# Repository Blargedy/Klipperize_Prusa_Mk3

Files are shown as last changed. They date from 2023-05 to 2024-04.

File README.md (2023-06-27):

# Klipperize Prusa Mk3
This repo is for sharing the results of my efforts to upgrade the performance of my Prusa Mk3s. It is not a project aimed at mass adoption and therfore does not include modularity for individual variations in component selection.

That being said, I designed the printer to use the [Rapid Burner](https://github.com/chirpy2605/voron/tree/main/V0/Rapid_Burner) by [chirpy2605 aka waytotheweb](https://github.com/chirpy2605), which is designed to work with the Voron v0.2. This means that my mods will work with any design that is compatible with the Voron v0.2 tool mount. Chirpy has a wide array of options for hotends, fans, extruders, and LEDs, so by Chirpy's efforts my mod can accomodate most people's hardware choices. 

***This project is still a work-in-progress, so expect files to change until I am satisfied with the result.*** 





**My hardware configuration is as follows:**
* Rapid Burner in slideswipe configuration
* Rapido UHF
* Sherpa Mini with RIDGA modification
* EBB36 CANbus toolhead PCB
* SKR mini e3 v2
* Raspberry Pi 4 running Klipper

## Benefits
* The stock prusa toolhead weighs 550g, depending on how you weigh the wires and bearings. The Prusa adapted Rapid Burner weighs 334g, a weight saving of 216g
* The stock E3D V6 hotend has a volumetric flow limit of around 20 mm<sup>3</sup>/s, 25 mm<sup>3</sup>/s with a CHT nozzle. The Rapido UHF, with a 0.4mm Volcano nozzle has a flow limit of 24.1 mm<sup>3</sup>/s, 29 mm<sup>3</sup>/s with a CHT nozzle. Higher flow rate means faster prints. 
* Input Shaping
* Fan headers allow more fans, and are easy to control with software
* Klipper's error logging is extensive, unlike prusa's error logging
* Macros
* The part cooling fans of the Rapid Burner are stronger than the Mk3's single blower fan
* RGBLEDs go brr
* Can use buttons as triggers for code, making predetermined tasks such as preheat much faster
* Filament diameter compensation
* Easier object exclusion
* Finer control on heater/stepper turn off
* Wait on chamber thermistor for automatic chamber heating
* Finer control over bed mesh pattern

## BoM
* 3 x MLX 42021 female crimp 2 circuit recepticle [Digikey](https://www.digikey.ca/en/products/detail/molex/0050841020/134710)
* 3 x MLX 42022 male crimp 2 circuit recepticle [Digikey](https://www.digikey.ca/en/products/detail/molex/0050842022/2405413)
* 1 x MLX 42021 female crimp 4 circuit recepticle [Digikey](https://www.digikey.ca/en/products/detail/molex/0050841045/2405428)
* 1 x MLX 42022 male crimp 4 circuit recepticle [Digikey](https://www.digikey.ca/en/products/detail/molex/0050842042/2405411)
* 10 x MLX 36536 male crimps [Digikey](https://www.digikey.ca/en/products/detail/molex/0365360001/3185301)
* 10 x MLX 36535 female crimps [Digikey](https://www.digikey.ca/en/products/detail/molex/0365350001/3185298)
* ~1m 16awg wire (two colors)
* ~50cm 18awg wire (two colors)
* ~1m 20/22awg wire (three or more colors)
* 1 x SKR Mini e3 v2
* 1 x Raspberry pi 3/4
* 1 x BigTreeTech U2C 
* 1 x BigTreeTech EBB36 CANbus
* 1 x 140mm Fan
* 16cm x 25cm mosquito net or wide pored cloth
* 2 pin microfit 3 connectors
* 4 pin microfit 3 connectors
* 12 pin microfit 3 connectors
* 14 pin microfit 3 connectors
* 4 x 6mmx3mm circular magnets
* M3 Hardware

## Printing Notes
* add negative volumes to the edges of the x axis ends
  

## Suggestions
* when soldering leads onto the bead thermistor that goes into the heat creep sensing pocket, try to make the solder joint as thin as possible, or you'll encounter clearance issues with the cable channel

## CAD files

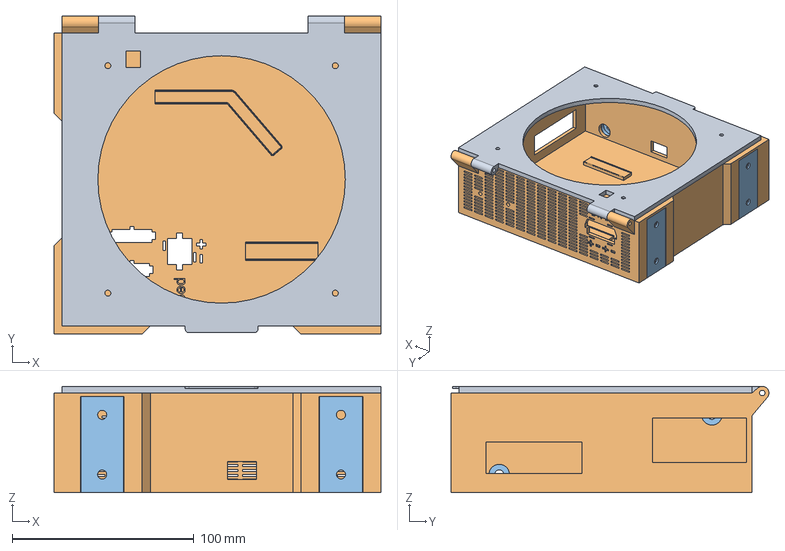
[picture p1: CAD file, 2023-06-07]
CAD/external_enclosure.step
179.7 x 174.7 x 58.5 mm

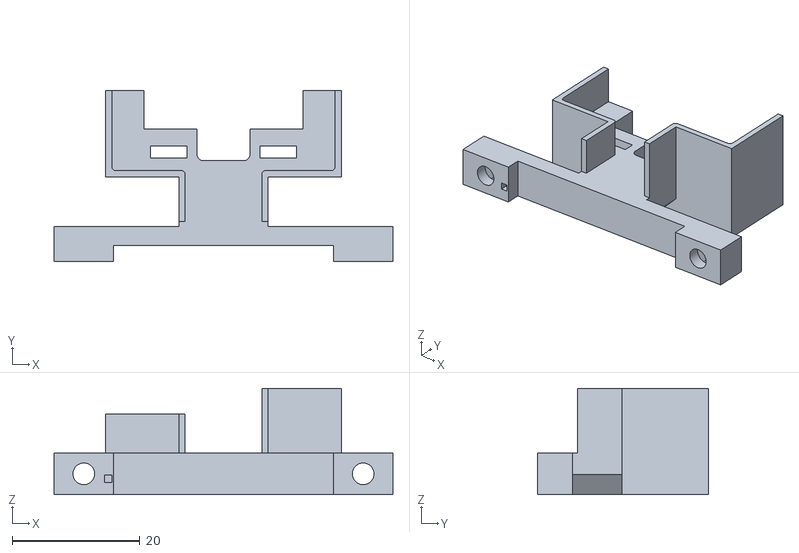
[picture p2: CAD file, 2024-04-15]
STLs/X_Carriage_EBB36_Standoff.stl
53.2 x 26.8 x 16.7

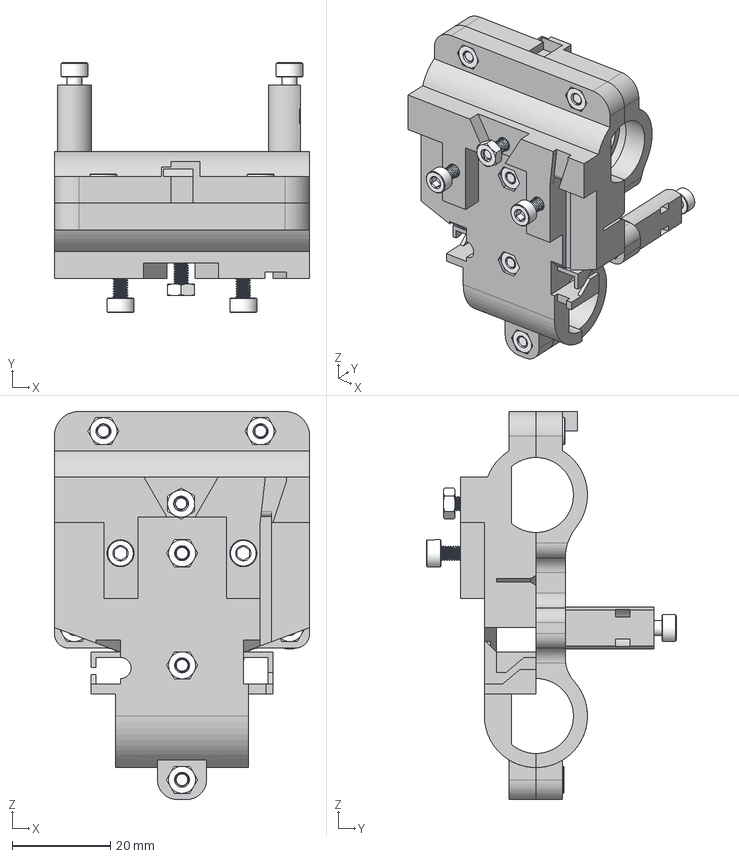
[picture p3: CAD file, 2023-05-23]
CAD/x_carriage.step
52.0 x 51.0 x 79.0 mm
CANbus Spacer 1
CANbus Spacer 2
M3 Hex Nut x 10
M3x8 BHCS
M3x12 SHCS x 2
M3x8 SHCS (1) x 2
M3x18 SHCS x 2
M3x25 SHCS x 2
M3x8 SHCS

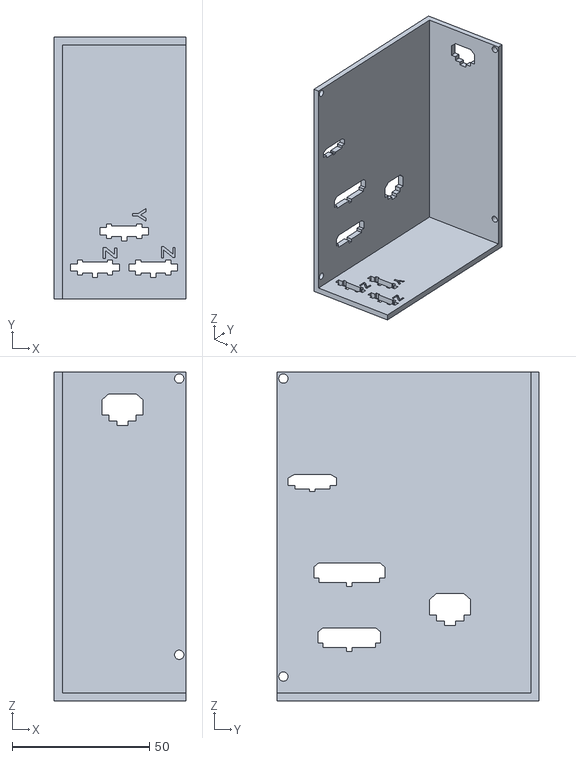
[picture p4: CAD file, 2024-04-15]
STLs/Internal_Enclosure_Connector_Half.stl
48.0 x 95.7 x 120.0

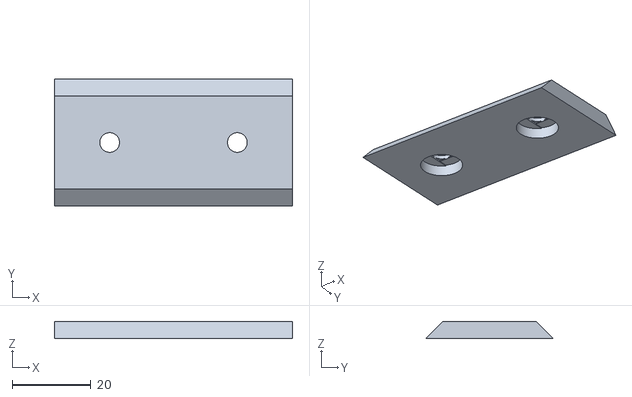
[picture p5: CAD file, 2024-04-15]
STLs/External_Enclosure_Rail_x4.stl
60.4 x 32.3 x 4.35

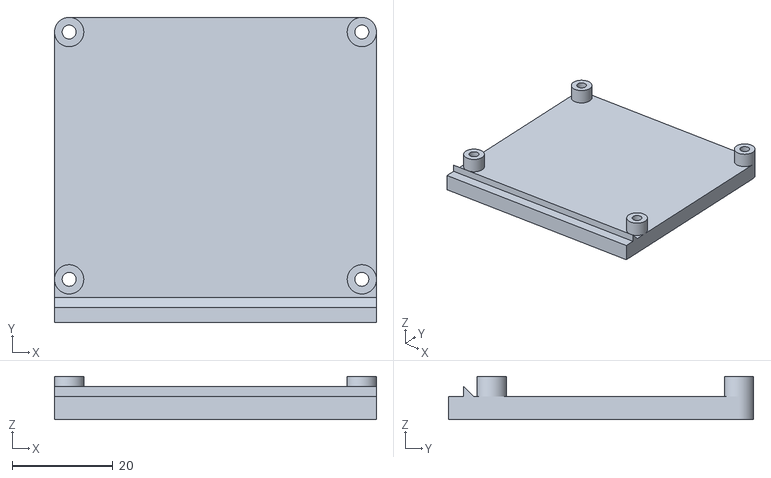
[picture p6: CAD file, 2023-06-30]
STLs/External_Enclosure_Rpi_Mount.stl
63.8 x 60.5 x 8.60

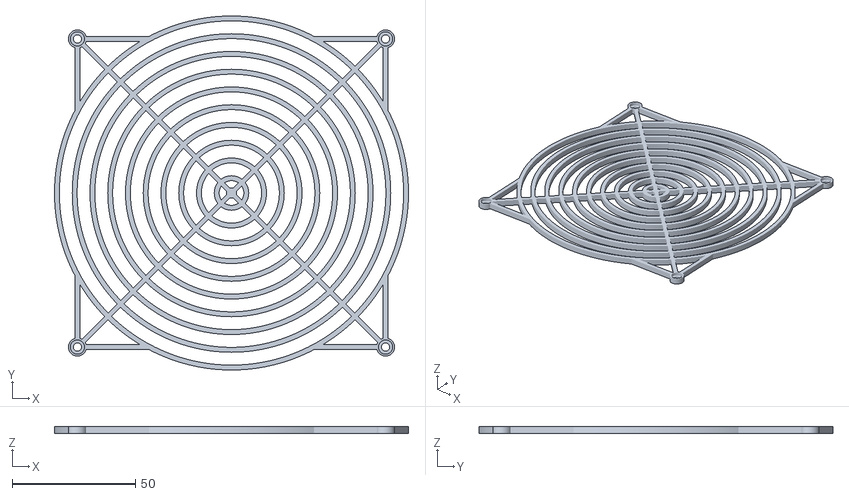
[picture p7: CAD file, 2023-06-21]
STLs/External_Enclosure_Fan_Grille.stl
143.6 x 143.6 x 3.00

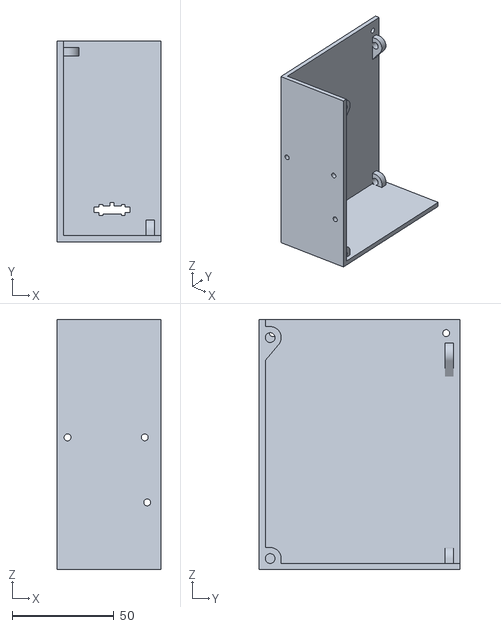
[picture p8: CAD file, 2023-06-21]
STLs/Internal_Enclosure_Printer_Mounted_Half.stl
51.0 x 98.7 x 123.0

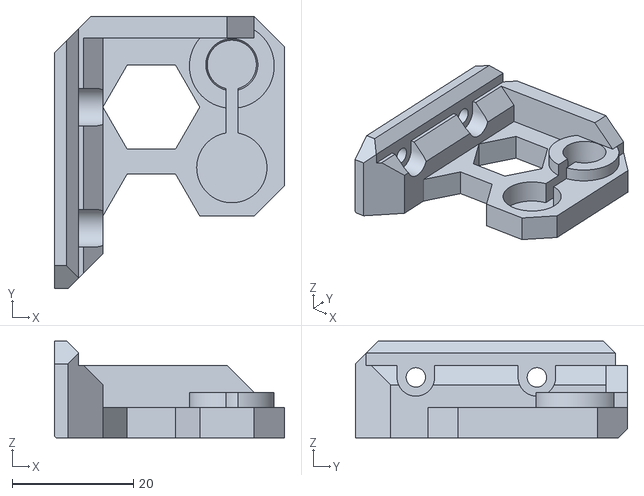
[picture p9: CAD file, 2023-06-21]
STLs/Z_Axis_Top_Left.stl
38.0 x 45.0 x 16.0

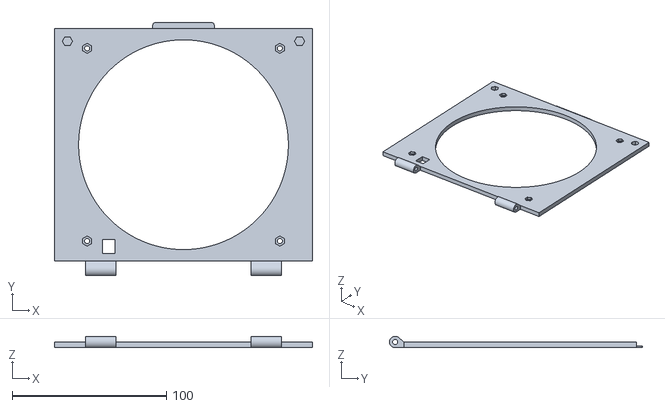
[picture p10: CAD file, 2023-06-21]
STLs/External_Enclosure_Lid.stl
167.3 x 164.2 x 7.40

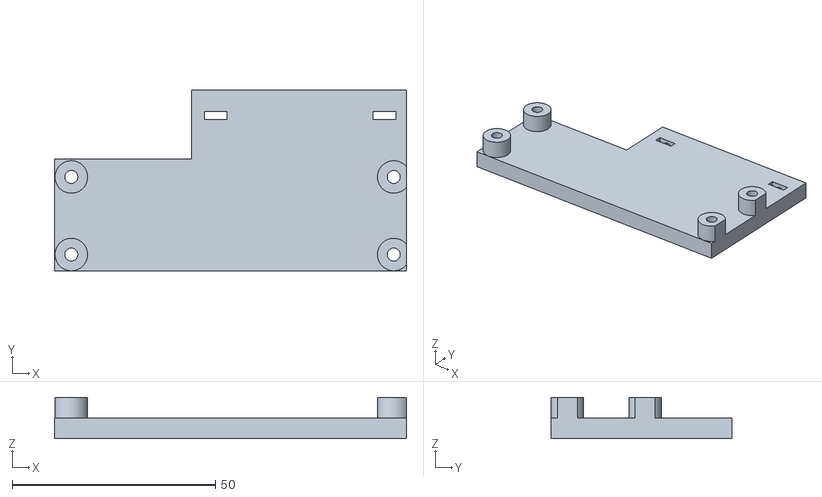
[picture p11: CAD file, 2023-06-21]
STLs/External_Enclosure_U2C_Holder.stl
86.6 x 44.7 x 10.1

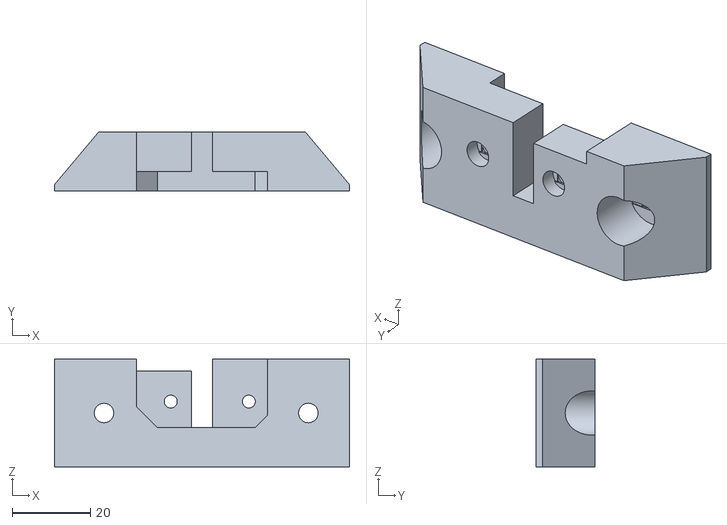
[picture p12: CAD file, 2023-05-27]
STLs/PSU_Upper_Mount.stl
75.5 x 15.0 x 27.5

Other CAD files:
STLs/Z_Axis_Top_Right.stl

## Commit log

2023-05-23 add existing tested files
    [SKR_holder.stl, Toolhead PCB Standoffs x2.stl, rpi_holder.stl]
2023-05-23 fixed STL orientation, naming, and file location
    [External_Enclosure_Face_Plate.stl, SKR_holder.stl, Toolhead PCB Standoffs x2.stl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]
2023-05-27 moved to single body enclosure
    [External_Enclosure_Face_Plate.stl]
2023-05-27 Mounts for the PSU attached to leg corner
    [PSU_Upper_Mount.stl]
2023-06-04 confirmed friction fit clearance
    [External_Enclosure_Rail_x4.stl]
2023-06-07 create fan grill to protect fan blades
    [External_Enclosure_Fan_Grill.stl]
2023-06-07 verified design and clearances
    [External_Enclosure_U2C_Holder.stl]
2023-06-07 add stp file for modder convenience
    [external_enclosure.step]
2023-06-09 chonkify grille
    [External_Enclosure_Fan_Grill.stl]
2023-06-09 spelling is hard
    [External_Enclosure_Fan_Grille.stl]
2023-06-21 Integrate standoffs for SKR and RPi into main body
    [External_Enclosure_Rpi_Holder.stl, External_Enclosure_SKR_holder.stl, External_Enclosure_U2C_Holder.stl]
2023-06-21 switch to molex minifit jr for power. Fix blocked access
    [External_Enclosure_Lid.stl, External_Enclosure_Rail_x4.stl]
2023-06-21 fix interference with x carriage and z axis top pieces
    [Z_Axis_Top_Left.stl, Z_Axis_Top_Right.stl]
2023-06-21 verified internal enclosure printer half
    [Internal_Enclosure_Printer_Mounted_Half.stl]
2023-06-21 increase heat break thermistor wire channel. Thicken fan grille
    [External_Enclosure_Fan_Grille.stl]
2023-06-30 moved rpi vertical to fix unreachable rpi power
    [External_Enclosure_Rpi_Mount.stl]
2024-04-15 idr lel
    [External_Enclosure_Rail_x4.stl, Internal_Enclosure_Connector_Half.stl, Toolhead_PCB_Standoffs_x2.stl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]
